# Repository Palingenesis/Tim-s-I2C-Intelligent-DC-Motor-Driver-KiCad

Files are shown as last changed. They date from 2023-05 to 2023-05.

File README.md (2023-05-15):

# Tim-s-I2C-Intelligent-DC-Motor-Driver-KiCad<br>
<br>
This is my Intelligent I2C DC Motor Driver<br>
It is an STM8S103F3P6 cofigured as an I2C Slave to control a DC Motor using a H Bridge.<br>
It can recives signals from Quadratic Encoder to determin direction and position.<br>
Also with a Quadratic Encoder attached you can set soft limits.<br>
There are pinouts to add hard stops<br>
There is a pinout to add a Station to set a known position<br>
Details: https://www.hackster.io/Tim_Palingenesis/tim-s-i2c-intelligent-dc-motor-driver-82cda1

<picture>
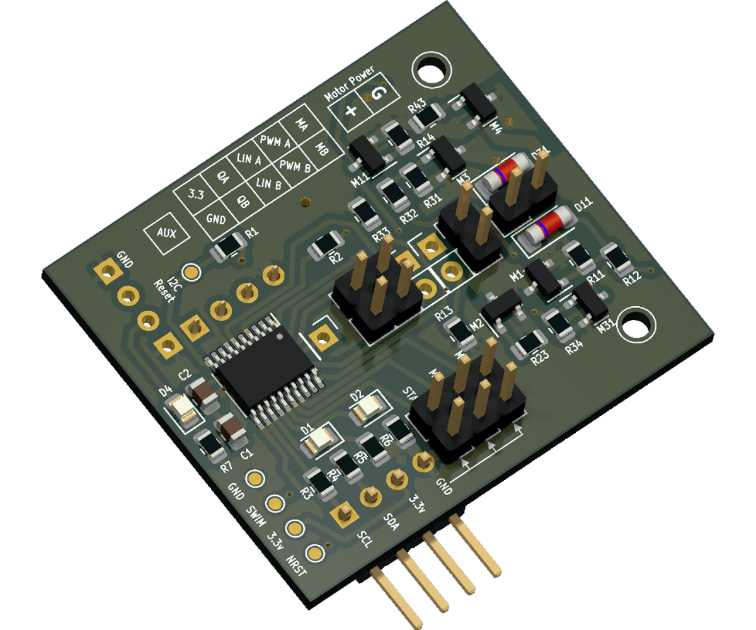
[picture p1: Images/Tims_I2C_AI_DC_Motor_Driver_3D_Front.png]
Tims I2C AI DC Motor Driver
  
</picture>

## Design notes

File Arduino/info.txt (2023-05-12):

Arduino files to test and configure the Motor Drivers.

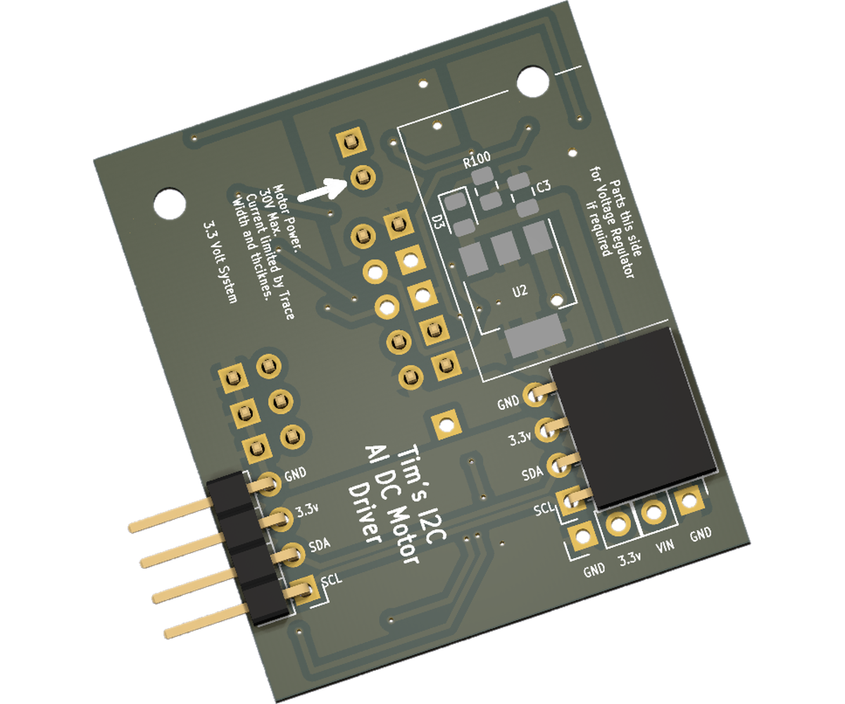
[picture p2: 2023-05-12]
Images/Tims_I2C_AI_DC_Motor_Driver_3D_Back_no_SMD.png

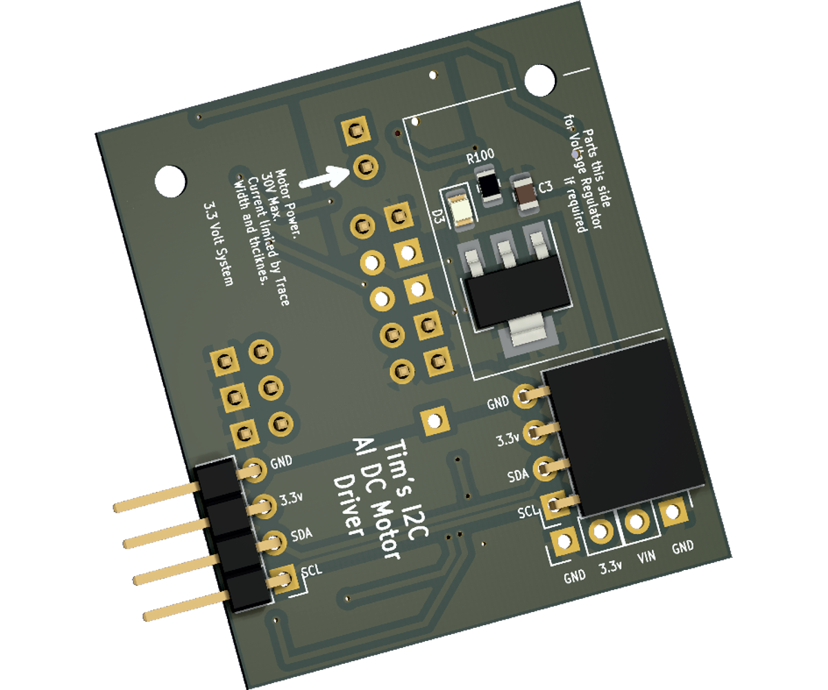
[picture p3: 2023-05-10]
Images/Tims_I2C_AI_DC_Motor_Driver_3D_Back.png

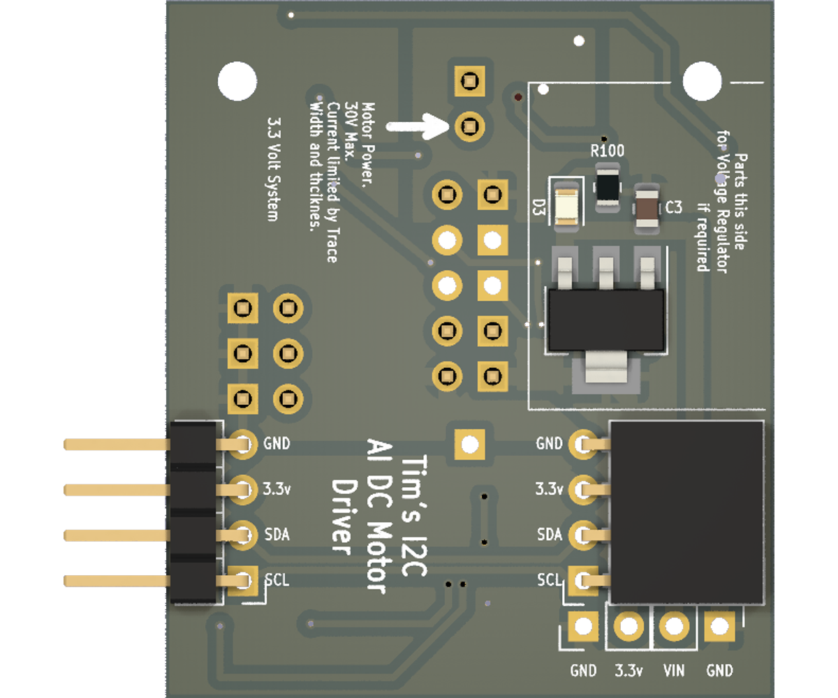
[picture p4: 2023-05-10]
Images/Tims_I2C_AI_DC_Motor_Driver_Back.png

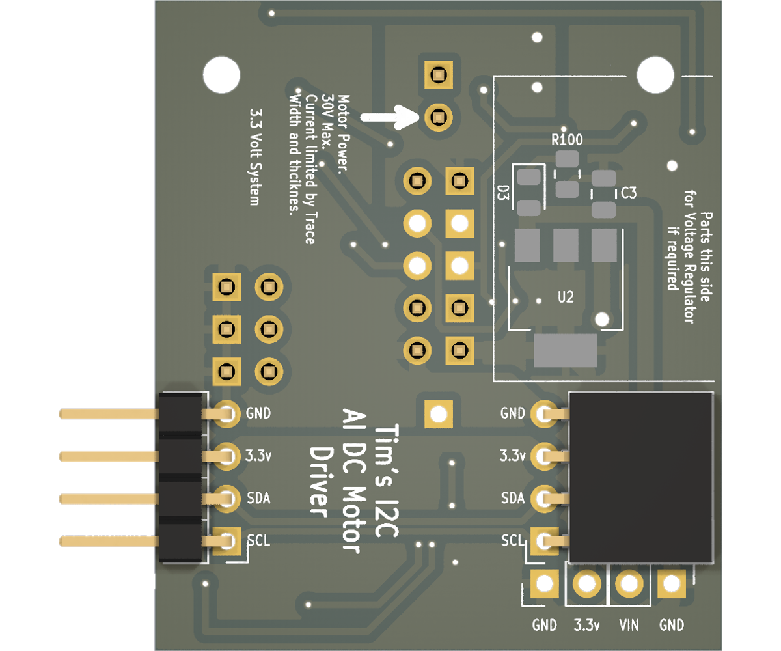
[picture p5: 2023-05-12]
Images/Tims_I2C_AI_DC_Motor_Driver 2P 2N Back no SMD.png

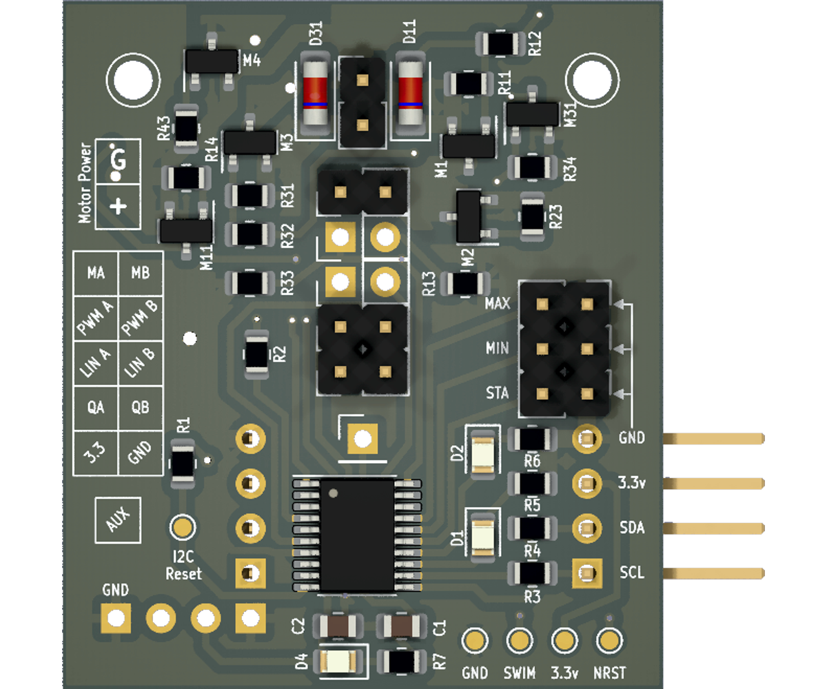
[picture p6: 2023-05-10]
Images/Tims_I2C_AI_DC_Motor_Driver_Front.png

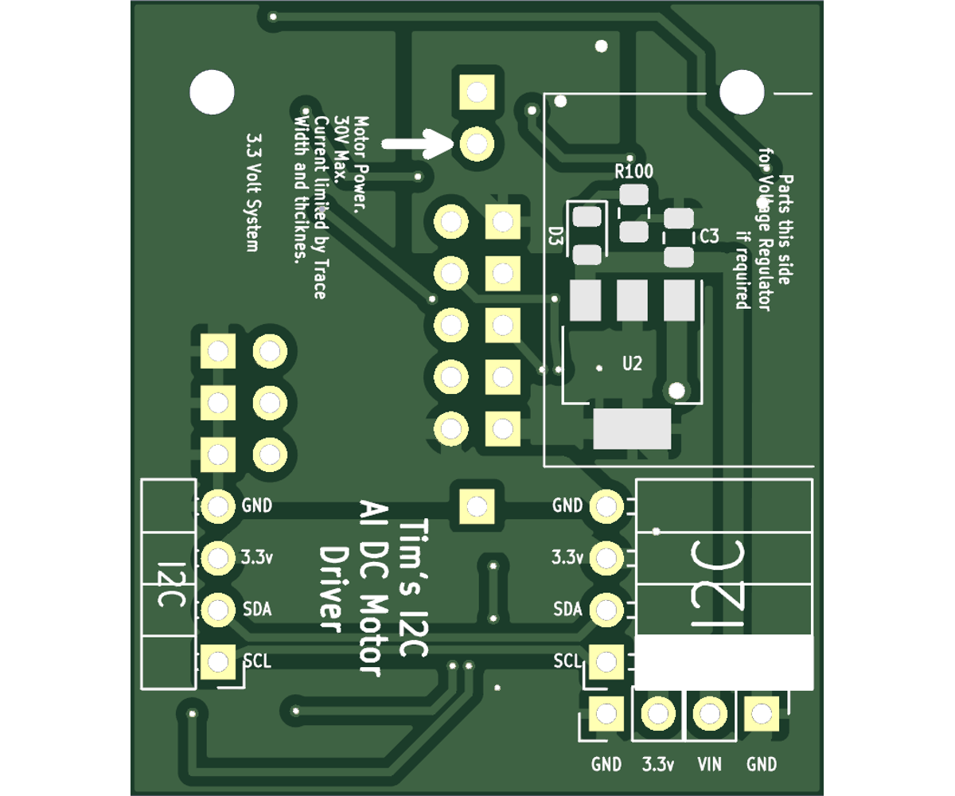
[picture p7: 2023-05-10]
Images/Tims_I2C_AI_DC_Motor_Driver_Back PCB.png

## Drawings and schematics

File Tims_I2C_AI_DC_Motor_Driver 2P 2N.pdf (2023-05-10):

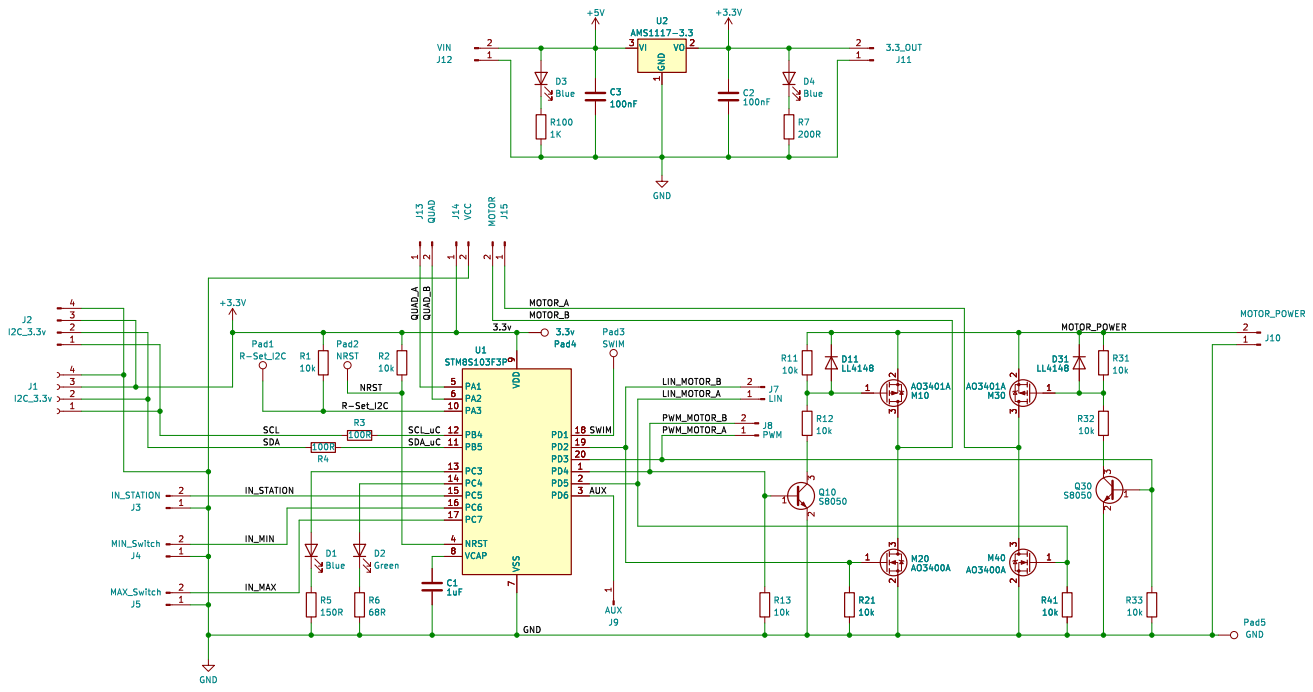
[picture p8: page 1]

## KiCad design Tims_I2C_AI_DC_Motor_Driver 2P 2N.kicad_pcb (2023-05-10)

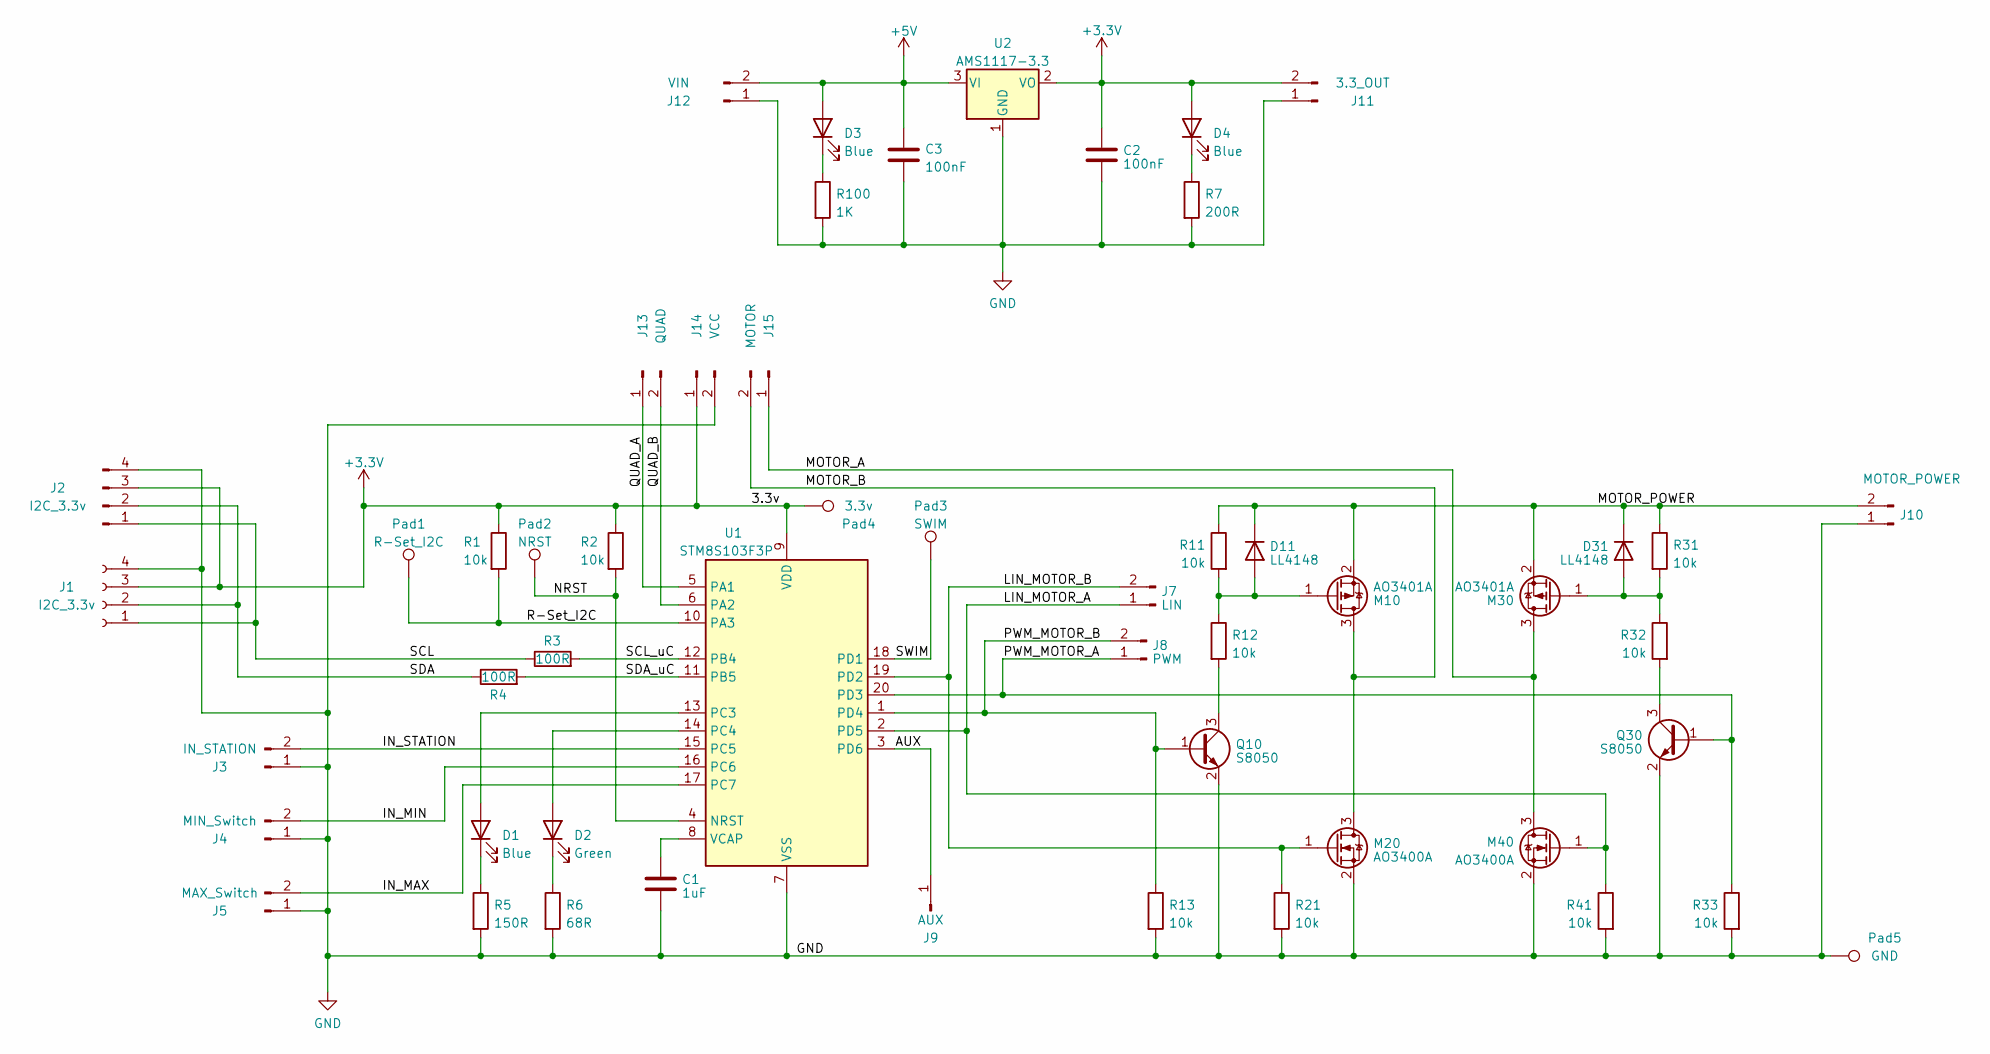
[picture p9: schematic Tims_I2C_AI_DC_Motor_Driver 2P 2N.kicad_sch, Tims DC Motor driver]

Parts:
C1: 1uF; C_0805_2012Metric
C2, C3: 100nF; C_0805_2012Metric
D1, D3, D4: Blue; LED_0805_2012Metric
D2: Green; LED_0805_2012Metric
D11, D31: LL4148; D_MiniMELF
J1: I2C_3.3v; PinSocket_1x04_P2.54mm_Horizontal
J2: I2C_3.3v; PinHeader_1x04_P2.54mm_Horizontal
J3: IN_STATION; PinHeader_1x02_P2.54mm_Vertical
J4: MIN_Switch; PinHeader_1x02_P2.54mm_Vertical
J5: MAX_Switch; PinHeader_1x02_P2.54mm_Vertical
J7: LIN; PinHeader_1x02_P2.54mm_Vertical
J8: PWM; PinHeader_1x02_P2.54mm_Vertical
J9: AUX; PinHeader_1x01_P2.54mm_Vertical
J10: MOTOR_POWER; PinHeader_1x02_P2.54mm_Vertical
J11: 3.3_OUT; PinHeader_1x02_P2.54mm_Vertical
J12: VIN; PinHeader_1x02_P2.54mm_Vertical
J13: QUAD; PinHeader_1x02_P2.54mm_Vertical
J14: VCC; PinHeader_1x02_P2.54mm_Vertical
J15: MOTOR; PinHeader_1x02_P2.54mm_Vertical
M10, M30: AO3401A; SOT-23
M20, M40: AO3400A; SOT-23
Pad1: R-Set_I2C; TestPoint_Pad_D1.0mm
Pad2: NRST; TestPoint_Pad_D1.0mm
Pad3: SWIM; TestPoint_Pad_D1.0mm
Pad4: 3.3v; TestPoint_Pad_D1.0mm
Pad5: GND; TestPoint_Pad_D1.0mm
Q10, Q30: S8050; SOT-23
R1, R2, R11, R12, R13, R21, R31, R32, R33, R41: 10k; R_0805_2012Metric
R3, R4: 100R; R_0805_2012Metric
R5: 150R; R_0805_2012Metric
R6: 68R; R_0805_2012Metric
R7: 200R; R_0805_2012Metric
R100: 1K; R_0805_2012Metric
U1: STM8S103F3P; TSSOP-20_4.4x6.5mm_P0.65mm
U2: AMS1117-3.3; SOT-223-3_TabPin2

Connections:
+3V3: C2.1, D4.2 (A), J1.3, J2.3, J11.2, J14.1, Pad4.1, R1.1, R2.1, U1.9 (VDD), U2.2 (VO)
+5V: C3.1, D3.2 (A), J12.2, U2.3 (VI)
/AUX: J9.1, U1.3 (PD6)
/IN_MAX: J5.2, U1.17 (PC7)
/IN_MIN: J4.2, U1.16 (PC6)
/IN_STATION: J3.2, U1.15 (PC5)
/LIN_MOTOR_A: J7.1, M40.1 (G), R41.1, U1.2 (PD5)
/LIN_MOTOR_B: J7.2, M20.1 (G), R21.1, U1.19 (PD2)
/MOTOR_A: J15.1, M30.3 (D), M40.3 (D)
/MOTOR_B: J15.2, M10.3 (D), M20.3 (D)
/MOTOR_POWER: D11.1 (K), D31.1 (K), J10.2, M10.2 (S), M30.2 (S), R11.1, R31.1
/NRST: Pad2.1, R2.2, U1.4 (NRST)
/PWM_MOTOR_A: J8.1, Q30.1 (B), R33.1, U1.20 (PD3)
/PWM_MOTOR_B: J8.2, Q10.1 (B), R13.1, U1.1 (PD4)
/QUAD_A: J13.1, U1.5 (PA1)
/QUAD_B: J13.2, U1.6 (PA2)
/R-Set_I2C: Pad1.1, R1.2, U1.10 (PA3)
/SCL: J1.1, J2.1, R3.1
/SCL_uC: R3.2, U1.12 (PB4)
/SDA: J1.2, J2.2, R4.1
/SDA_uC: R4.2, U1.11 (PB5)
/SWIM: Pad3.1, U1.18 (PD1)
GND: C1.2, C2.2, C3.2, J1.4, J2.4, J3.1, J4.1, J5.1, J10.1, J11.1, J12.1, J14.2, M20.2 (S), M40.2 (S), Pad5.1, Q10.2 (E), Q30.2 (E), R5.2, R6.2, R7.2, R13.2, R21.2, R33.2, R41.2, R100.2, U1.7 (VSS), U2.1 (GND)
unnamed: D1.2 (A), U1.13 (PC3)
unnamed: D1.1 (K), R5.1
unnamed: D2.2 (A), U1.14 (PC4)
unnamed: D2.1 (K), R6.1
unnamed: D3.1 (K), R100.1
unnamed: D4.1 (K), R7.1
unnamed: D11.2 (A), M10.1 (G), R11.2, R12.1
unnamed: D31.2 (A), M30.1 (G), R31.2, R32.1
unnamed: Q10.3 (C), R12.2
unnamed: Q30.3 (C), R32.2
unnamed: C1.1, U1.8 (VCAP)

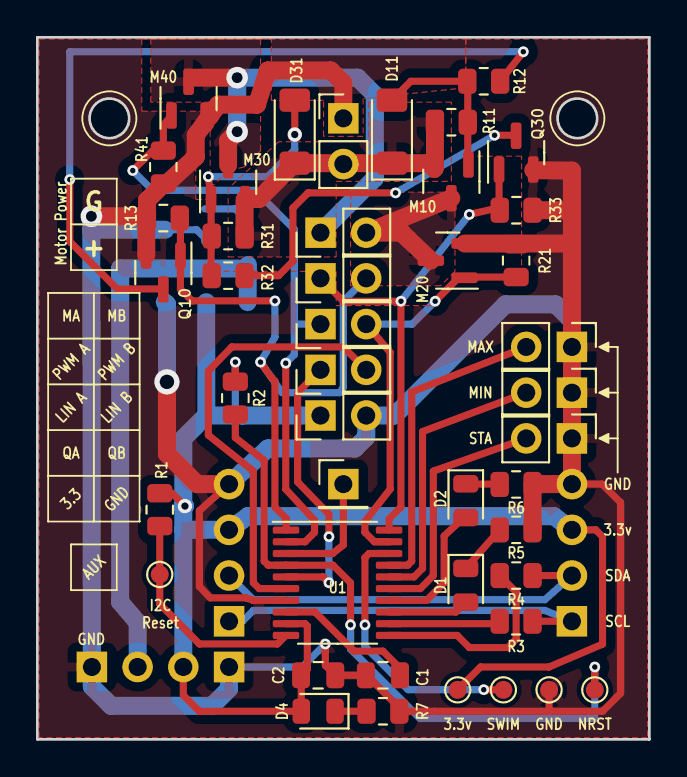
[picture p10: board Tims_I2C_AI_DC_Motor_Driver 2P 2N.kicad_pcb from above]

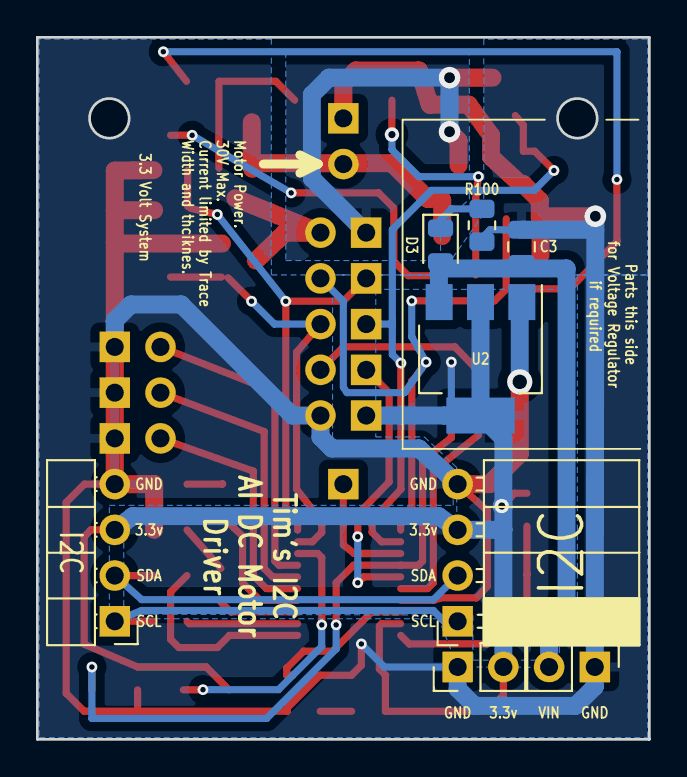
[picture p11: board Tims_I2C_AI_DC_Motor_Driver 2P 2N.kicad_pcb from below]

Board: 2 copper layers, 34.0 x 39.0 mm, 52 parts (8 on the bottom side), 34 nets.

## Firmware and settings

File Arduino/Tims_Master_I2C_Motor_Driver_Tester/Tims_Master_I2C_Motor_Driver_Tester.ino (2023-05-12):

/*
	A small program to send commands via Serial to Tim's I2C Intelligent DC Motor Driver.

	By Tim Jackson.1960
		More info on Instructables. https://www.instructables.com/member/Palingenesis/instructables/

	This Sketch was written for the Arduino Nano 33 IoT. But should work on any Arduino Device.

	Arduino SAMD21.
		Sketch uses 16312 bytes (6%) of program storage space. Maximum is 262144 bytes.
		Global variables use 4616 bytes (14%) of dynamic memory, leaving 28152 bytes for local variables. Maximum is 32768 bytes.

	Arduino ATmega328.
		Sketch uses 5990 bytes (19%) of program storage space. Maximum is 30720 bytes.
		Global variables use 946 bytes (46%) of dynamic memory, leaving 1102 bytes for local variables. Maximum is 2048 bytes.

	ESP8266 (2M SPIFFS)
	Sketch uses 270796 bytes (25%) of program storage space. Maximum is 1044464 bytes.
	Global variables use 27972 bytes (34%) of dynamic memory, leaving 53948 bytes for local variables. Maximum is 81920 bytes.



	Wire request buffer of the Motor Driver was originaly set/configured for 32 bit values but was reduced to 24+ bit numbers.
	The original code is commented out should I change microcontroller with more memory.
	I say 24+ bit number becouse I have used a seperate Byte for negative flags.
	This gives a number range of: -16,777,215 to 16,777,215.
	To make it more universal, all values are Ticks of the Motors Quadratic Encoder.

	Wire_Request converts as follows:

		1st byte Flags_1 true if:
			LSB		1	=	CurPossition < 0
					2	=	MaxPossition < 0
					4	=	MinPossition < 0
					8	=	Station_F < 0
					16	=	Station_R < 0
					32	=	HasMAX
					64	=	HasMIN
			MSB		128	=	HasStaton

		2nd byte Flags_2 true if:
			LSB		1	=	MIN_Hit
					2	=	MAX_Hit
					4	=
					8	=
					16	=
					32	=
					64	=
			MSB		128	=

		bytes 3 to 6 Current position.
			CurPossition	LSB1
			CurPossition	LSB2
			CurPossition	MSB1
			CurPossition	MSB2
		byte 7 I2C Addres of device. (The Address Arduino uses to talk to the device)
			My_I2C_Address
		bytes 8 and 9 Motor Slowdown point.
			Motor_Slowdown_point LSB
			Motor_Slowdown_point MSB
		bytes 10 to 13 Max position.
			MaxPossition	LSB1
			MaxPossition	LSB2
			MaxPossition	MSB1
			MaxPossition	MSB2
		bytes 14 to 17 Min position.
			MinPossition	LSB1
			MinPossition	LSB2
			MinPossition	MSB1
			MinPossition	MSB2
		bytes 18 to 21 Station Moving Forward position.
			Station_F		LSB1
			Station_F		LSB2
			Station_F		MSB1
			Station_F		MSB2
		bytes 22 to 25 Station Moving Reverse position.
			Station_R		LSB1
			Station_R		LSB2
			Station_R		MSB1
			Station_R		MSB2
		byte 26 Motor Speed Reduction percentage when comming to a stop.
			Motor_Speed_Reduction

	The buffer holds 32 bytes, the rest are not used.
		Currently hold data version an maker.

*/

#include <Wire.h>

//#define TARGET_I2C_ADDRESS	0x30    /*  0x30=48 0x60=96 0x32=50Target Address.	*/
int Target_I2C_Address = 0x30;

#define BUFF_64				64      /*  What is the longest message Arduino can store?	*/
#define BUFF_16				16
#define BUFF_24				24
#define BUFF_32				32

/*	SERIAL MESSAGES	*/
char Buffer_TX[BUFF_64];		/* message				*/
uint8_t Buffer_RX[BUFF_32];		/* message				*/
unsigned int no_data = 0;
unsigned int sofar;				/* size of Buffer_TX	*/
bool isComment = false;
bool procsessingString = false;
short cmd = -1;
bool slaveProcesing = false;
bool ProcsessingCommand = false;

/*	Debug	*/
long TimeNow = millis();
long Period = 1000;
long TimeOut = TimeNow + Period;

void setup() {
	/*
	  Start serial.
	*/
	Serial.begin(115200);
	/*
	  Start Wire.
		  Used only as Master atm. (address optional for master)
	*/
	Wire.begin();
	Wire.setClock(400000);
	Wire.onRequest(Wire_Request);

	/*	Debug	*/
	pinMode(LED_BUILTIN , OUTPUT);

}

void loop() {
	/*
		Tick - Tock
	*/
	TimeNow = millis();
	/*
		Get next command when finish current command.
	*/
	if (!procsessingString) { ReadSerial(); }

	if (TimeNow > TimeOut){
		TimeOut = TimeNow + Period;
		digitalWrite(LED_BUILTIN , !digitalRead(LED_BUILTIN ));
	}

}
/*
	Read Data in Serial Buffer if available.
*/
void ReadSerial() {
	/*
		Holder
	*/
	char c;
	/*
		Read in characters if available.
	*/
	if (Serial.available() > 0) {
		c = Serial.read();
		no_data = 0;
		/*
			Chech for newlines.
		*/
		if (c != '\r' || c != '\n') {
			/*
				Check for comments.
					These are used in G-Code.
			*/
			if (c == '(' || c == ';') {
				isComment = true;
			}
			/*
				If we're not in "isComment" mode, add it to our array.
			*/
			if (!isComment) {
				Buffer_TX[sofar++] = c;
			}
			/*
				End of isComment - start listening again.
			*/
			if (c == ')') {
				isComment = false;
			}
		}
	}
	else {
		no_data++;
		delayMicroseconds(100); // 100
		/*
			Process any code that has been recived
		*/
		if (sofar && (c == '\n' || c == '\r' || no_data > 100)) {
			no_data = 0;
			sofar--;

#ifdef PRIN_SERIAL
			Serial.println(Buffer_TX);
			delay(50);
#endif  //  PRIN_SERIAL

			procsessingString = true;
			processCommand();
			init_process_string();
		}
	}

}
/*
	Set ready for next command.
*/
void init_process_string() {

	for (byte i = 0; i < BUFF_64; i++) { Buffer_TX[i] = 0; }
	sofar = 0;
	procsessingString = false;
	isComment = false;
	cmd = -1;
	Wire.flush();
	Serial.flush();
	Serial.println("ok");
	delay(4);
}
/*
	Change command numbers to a long.
*/
long Parse_Number(char code, long val) {
	/*
		start at the beginning of Buffer_TX.
	*/
	char* ptr = Buffer_TX;
	/*
	  Go char to char through string.
	*/
	while ((long)ptr > 1 && (*ptr) && (long)ptr < (long)Buffer_TX + sofar) {
		/*
			if you find code as you go through string.
		*/
		if (*ptr == code) {
			/*
				convert the digits that follow into a long and return it.
			*/
			return atol(ptr + 1);
		}
		/*
			take a step from here to the next char after the next space.
		*/
		ptr = strchr(ptr, ' ') + 1;
	}
	/*
		If the end is reached and nothing found, return val.
	*/
	return val;
}
/*
	Process Commands.
*/
void processCommand() {

	uint32_t _Val = 0;
	uint8_t _Flag1 = 0;
	uint8_t _Flag2 = 0;

	/*	Get I2C Address if given. (defalt 0x30 or last sent)	*/
	Target_I2C_Address = Parse_Number('D', Target_I2C_Address);

	/*	get start of Buffer_TX (see what the command starts with)	*/
	char* ptr = Buffer_TX; // 

	/*
		======================
		Chose GET, Process or SEND
		======================
	*/
	if (*ptr == 'X') {
		/*	GET	*/
		int _numberOfBytes = Parse_Number('X', -1);
		if (_numberOfBytes == 0) {
			_numberOfBytes = BUFF_32;
		}

		/*	Clear Buffer	*/
		for (size_t i = 0; i < BUFF_32; i++) {
			Buffer_RX[i] = 0;
		}

		Wire.requestFrom(Target_I2C_Address, _numberOfBytes);
		delayMicroseconds(5);

		if (Wire.available()) {
			/*	Read Buffer	*/
			for (size_t i = 0; i < _numberOfBytes; i++) {
				uint8_t C = Wire.read();
				Buffer_RX[i] = C;
				//Serial.print(C);
				//Serial.print(", ");
			}
			//Serial.println();
		}
		/*	Buffer in Binary	*/
		if (_numberOfBytes > 7) {
			for (size_t i = BUFF_32; i > 0; i--) {

				Serial.print("Buffer_RX[");
				Serial.print(i - 1);
				Serial.print("] \tBIN = ");
				Serial.println(Buffer_RX[i - 1], BIN);
			}
		}


		/*
			===============
			Use and Format Info
			===============
		*/

		/*	Slave_Buffer_Tx[7] = Flags	*/
		_Flag1 = Buffer_RX[0];
		if (Buffer_RX[6] == 0) {
			Serial.println();
			Serial.print("No Address ");
			Serial.print(Target_I2C_Address, DEC);
			Serial.print(" (0x");
			Serial.print(Target_I2C_Address, HEX);
			Serial.print(") found.");
			Serial.println();
		}
		else {
			Serial.println();
			Serial.println("Formated:");
			Serial.println();

			/*	Currrent Possition	*/
			//_Val = Buffer_RX[5];
			//_Val = _Val << 0x08;
			_Val |= Buffer_RX[4];
			_Val = _Val << 0x08;
			_Val |= Buffer_RX[3];
			_Val = _Val << 0x08;
			_Val |= Buffer_RX[2];
			Serial.print("Currrent Position\tDEC = ");
			_Flag1 = (Buffer_RX[0] & 1);
			if (_Flag1 == 1) { Serial.print("-"); }
			else { Serial.print(" "); }
			Serial.println(_Val, DEC);

			/*	Limit Switches	*/
			_Flag2 = (Buffer_RX[1] & 1);
			if (_Flag2 == 1) { Serial.println("MIN Stop Hit"); }
			else { Serial.println("MIN OK"); }
			_Flag2 = (Buffer_RX[1] & 2);
			if (_Flag2 == 2) { Serial.println("MAX Stop Hit"); }
			else { Serial.println("MAX OK"); }

			if (_numberOfBytes > 7) {

				/*	My_I2C_Address		*/
				Serial.print("I2C Address\t\t\tDEC =  ");
				Serial.print(Buffer_RX[6], DEC);
				Serial.print("(HEX = 0x");
				Serial.print(Buffer_RX[6], HEX);
				Serial.println(")");

				/*  I2C Speed  */
				Serial.print("I2C Speed\t\t\tDEC =  ");
				_Flag2 = (Buffer_RX[1] & 4);
				if (_Flag2 == 4) { Serial.println("400000"); }
				else { Serial.println("100000"); }


				/*	Motor_Slowdown		*/
				_Val = Buffer_RX[8];
				_Val = _Val << 0x08;
				_Val |= Buffer_RX[7];
				Serial.print("Motor Slowdown\t\tDEC =  ");
				Serial.println(_Val);

				/*	MaxPossition		*/
				//_Val = Buffer_RX[12];
				//_Val = _Val << 0x08;
				_Val = Buffer_RX[11];
				_Val = _Val << 0x08;
				_Val |= Buffer_RX[10];
				_Val = _Val << 0x08;
				_Val |= Buffer_RX[9];
				Serial.print("Max Possition    \tDEC = ");
				_Flag1 = (Buffer_RX[0] & 2);
				if (_Flag1 == 2) { Serial.print("-"); }
				else { Serial.print(" "); }
				Serial.println(_Val, DEC);

				/*	MinPossition		*/
				//_Val = Buffer_RX[16];
				//_Val = _Val << 0x08;
				_Val = Buffer_RX[15];
				_Val = _Val << 0x08;
				_Val |= Buffer_RX[14];
				_Val = _Val << 0x08;
				_Val |= Buffer_RX[13];
				Serial.print("Min Possition    \tDEC = ");
				_Flag1 = (Buffer_RX[0] & 4);
				if (_Flag1 == 4) { Serial.print("-"); }
				else { Serial.print(" "); }
				Serial.println(_Val, DEC);

				/*	Station F		*/
				//_Val = Buffer_RX[20];
				//_Val = _Val << 0x08;
				//_Val |= Buffer_RX[19];
				//_Val = _Val << 0x08;
				_Val = Buffer_RX[18];
				_Val = _Val << 0x08;
				_Val |= Buffer_RX[17];
				Serial.print("Station Forward\t\tDEC = ");
				_Flag1 = (Buffer_RX[0] & 8);
				if (_Flag1 == 8) { Serial.print("-"); }
				else { Serial.print(" "); }
				Serial.println(_Val, DEC);

				/*	Station R		*/
				//_Val = Buffer_RX[24];
				//_Val = _Val << 0x08;
				//_Val |= Buffer_RX[23];
				//_Val = _Val << 0x08;
				_Val = Buffer_RX[22];
				_Val = _Val << 0x08;
				_Val |= Buffer_RX[21];
				Serial.print("Station Reverse\t\tDEC = ");
				_Flag1 = (Buffer_RX[0] & 16);
				if (_Flag1 == 16) { Serial.print("-"); }
				else { Serial.print(" "); }
				Serial.println(_Val, DEC);

				/*	HasFlags		*/
				_Flag1 = (Buffer_RX[0] & 32);
				if (_Flag1 == 32) { Serial.println("\tHasMAX       = true"); }
				else { Serial.println("\tHasMAX       = false"); }
				_Flag1 = (Buffer_RX[0] & 64);
				if (_Flag1 == 64) { Serial.println("\tHasMIN       = true"); }
				else { Serial.println("\tHasMIN       = false"); }
				_Flag1 = (Buffer_RX[0] & 128);
				if (_Flag1 == 128) { Serial.println("\tHasStation   = true"); }
				else { Serial.println("\tHasStation   = false"); }

				/*	Motor Speed Reduction	*/
				Serial.print("Motor Speed Reduction = ");
				Serial.print(Buffer_RX[25]);
				Serial.println("%");

				/*	Tim			*/
				for (size_t i = 29; i < 32; i++) {
					Serial.print((char)Buffer_RX[i]);
				}
				Serial.println();

			}

			delayMicroseconds(5);
		}
	}
	else if (*ptr == 'P'){

	}
	else {
		/*	SEND	*/
		ProcsessingCommand = true;
		Wire.flush();
		SendBufferOnI2C(Target_I2C_Address);
		delay(4);
		ProcsessingCommand = false;

	}
}
/*
	Send Recived Commands on to a Device on the I2C bus.
*/
void SendBufferOnI2C(int I2C_address) {

	Wire.beginTransmission(I2C_address);	//	Get device at I2C_address attention
	Wire.write(Buffer_TX, sofar);			//	Send Buffer_TX
	Wire.endTransmission();					//	Stop transmitting

#ifdef PRIN_SERIAL
	Serial.print("Buffer_TX ");
	Serial.print(Buffer_TX);
	Serial.print("\tsofar ");
	Serial.println(sofar);
	delay(50);
#endif  //  PRIN_SERIAL

}
/*
	I2C Request Data
*/
void Wire_Request() {

}

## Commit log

2023-05-10 Add project files.
    [Tims_I2C_AI_DC_Motor_Driver 2P 2N-B_Cu.gbr, Tims_I2C_AI_DC_Motor_Driver 2P 2N-B_Mask.gbr, Tims_I2C_AI_DC_Motor_Driver 2P 2N-B_Paste.gbr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]
2023-05-12 Update BOM
    [Tims_I2C_AI_DC_Motor_Driver 2P 2N.csv]
2023-05-15 Update parts list
    [Tims_I2C_AI_DC_Motor_Driver 2P 2N Modified All.csv, Tims_I2C_AI_DC_Motor_Driver 2P 2N Parts Required.csv]
2023-05-15 Change BOM
    [Tims_I2C_AI_DC_Motor_Driver 2P 2N Modified All.csv, Tims_I2C_AI_DC_Motor_Driver 2P 2N Only Parts Required.csv, Tims_I2C_AI_DC_Motor_Driver 2P 2N.csv]
